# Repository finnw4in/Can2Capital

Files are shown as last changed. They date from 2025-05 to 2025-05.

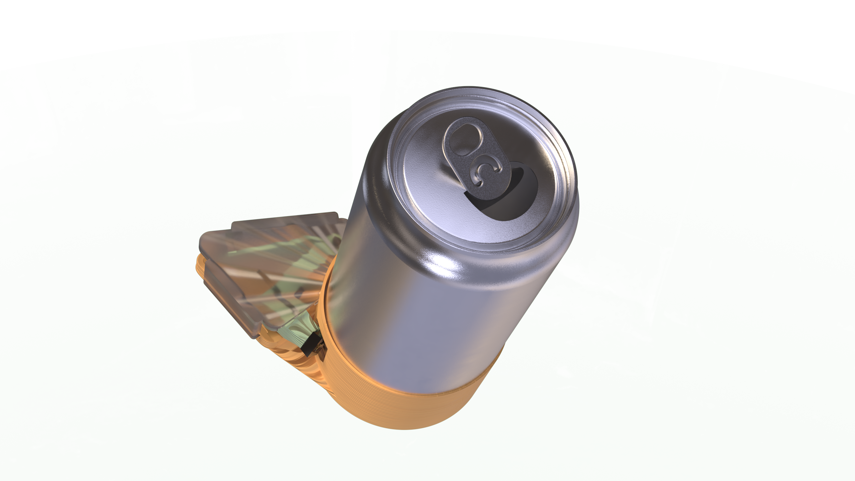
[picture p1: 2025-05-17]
images/BenchTop RenderV3.68.png

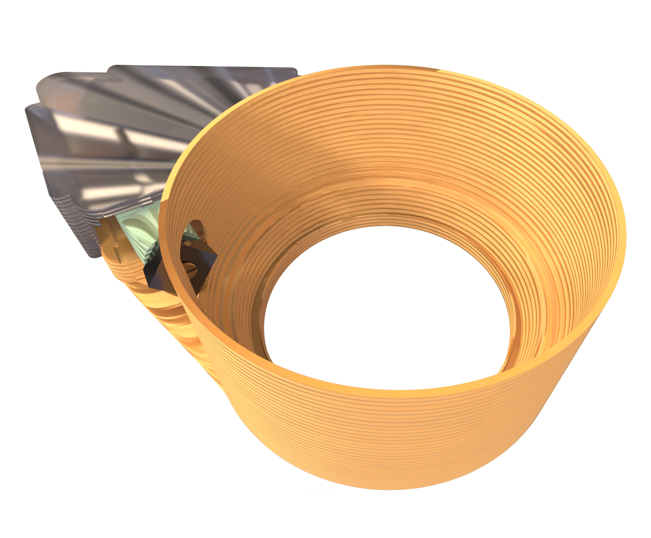
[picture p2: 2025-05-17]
images/BenchTop RenderV3.76.png

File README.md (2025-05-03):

title: Can-2-Capital
Date: 2025-05-03

# Can 2 Capital: A Decentralised Digital Kit

**Can 2 Capital** is a decentralised digital kit that enables anyone and everyone to turn waste aluminium cans into something valuable that can be sold, traded, or kept.

### How Does It Differ?
Can 2 Capital differs from traditional industrial aluminium recycling as it seeks to return **profit to the user**, not the producer.

---

### Powered by YOU:
- **100 Joules of Human Effort**
- **50g of PETG & Carbide Insert**

---

### Key Benefits:
- **28x Increase in Recycling Collection Efficiency**
- **Recycle with 99.8% Less Energy** than industrial recycling

---

Join the movement and make a difference with **Can 2 Capital** today!

## Phase One Download Files

- [Download 3DM Files](https://github.com/finnw4in/Can2Capital/tree/main/3dm-files)

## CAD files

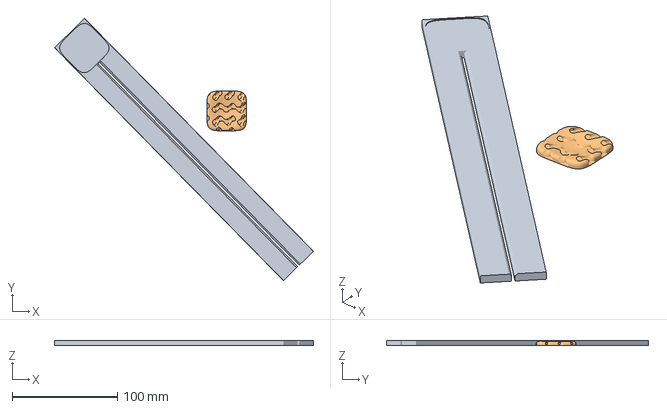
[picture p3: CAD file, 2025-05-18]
3dm-files/Can Finger Model.3mf
245.8 x 249.1 x 5.00 mm
Wain, F, Phase 1, Can-2-Capital-Stripper Can Finger.stl_10
Wain, F, Phase 1, Can-2-Capital-Stripper Can Finger.stl_11

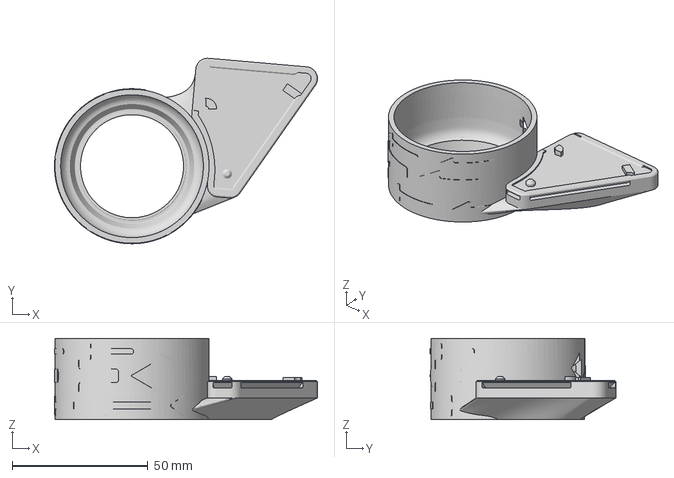
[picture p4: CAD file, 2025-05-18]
3dm-files/53mm Slim.3mf
97.0 x 68.5 x 30.0 mm

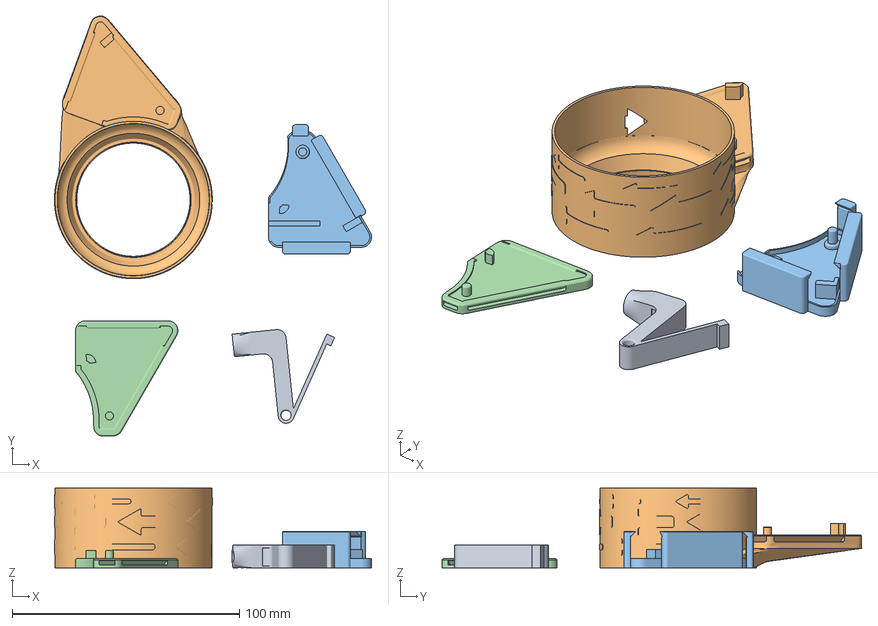
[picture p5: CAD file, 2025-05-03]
3dm-files/Can-2-Capital-Stripper Tool-V11.3mf
139.6 x 184.9 x 35.0 mm
V10.5 Spring Mech v1 v2
V11.5 Lower .step
v11 plate v1.step

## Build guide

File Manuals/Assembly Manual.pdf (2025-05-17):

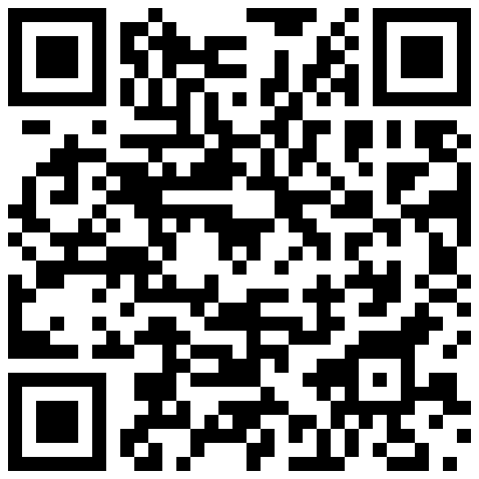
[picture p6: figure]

# Can 2 Capital Can Stripper Assembly Guide ENGLISH

3

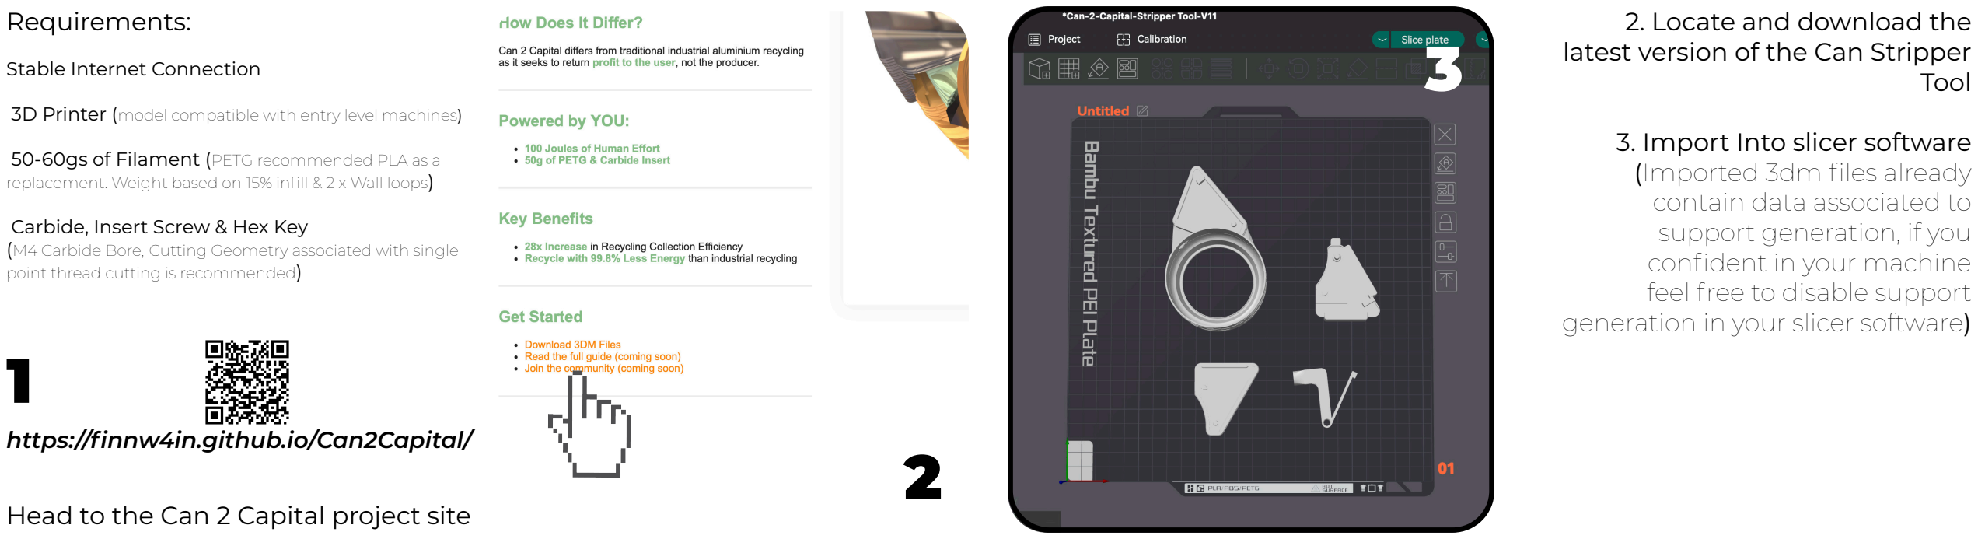
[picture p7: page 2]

2. Locate and download the latest version of the Can Stripper Tool
3. Import Into slicer software (Imported 3dm files already

contain data associated to support generation, if you confident in your machine
feel free to disable support generation in your slicer software

)
2

https://finnw4in.github.io/Can2Capital/ 1

Head to the Can 2 Capital project site

Requirements:

Stable Internet Connection

3D Printer (model compatible with entry level machines )

50-60gs of Filament (PETG recommended PLA as a replacement. Weight based on 15% infill & 2 x Wall loops

)

Carbide, Insert Screw & Hex Key (M4 Carbide Bore, Cutting Geometry associated with single

point thread cutting is recommended

)

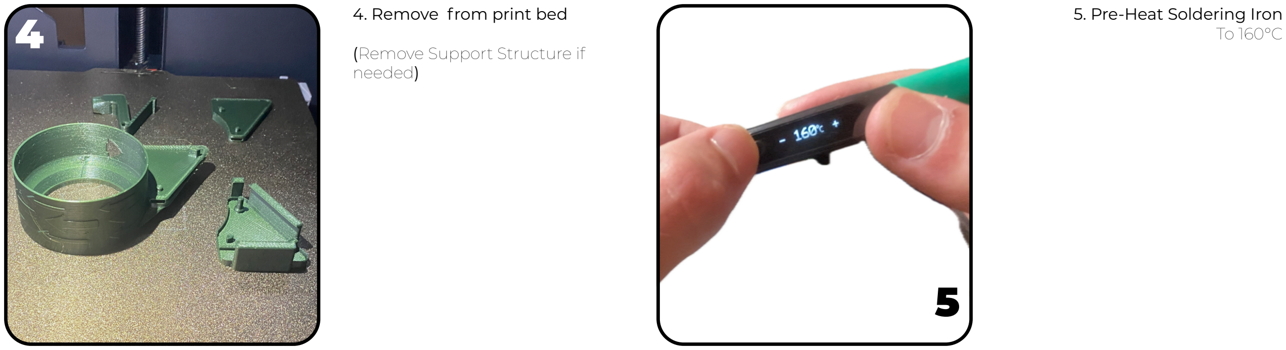
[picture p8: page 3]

4. Remove from print bed

(Remove Support Structure if needed)

5. Pre-Heat Soldering Iron

### 4 To 160°C

5

6

7

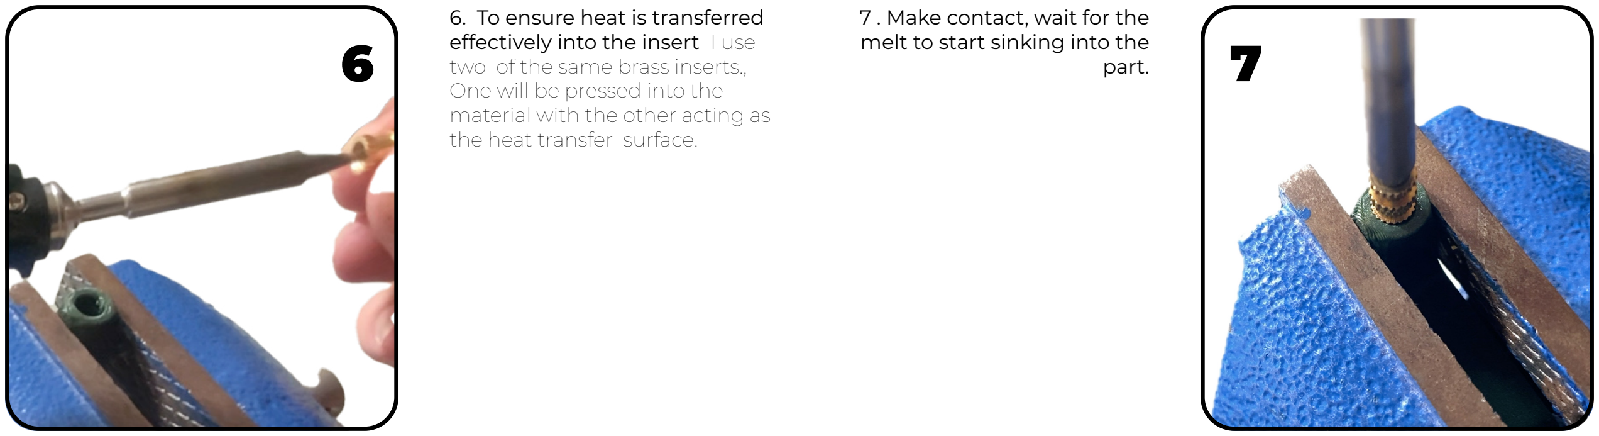
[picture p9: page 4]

6. To ensure heat is transferred effectively into the insert I use two of the same brass inserts., One will be pressed into the material with the other acting as the heat transfer surface.

7 . Make contact, wait for the melt to start sinking into the part.

9

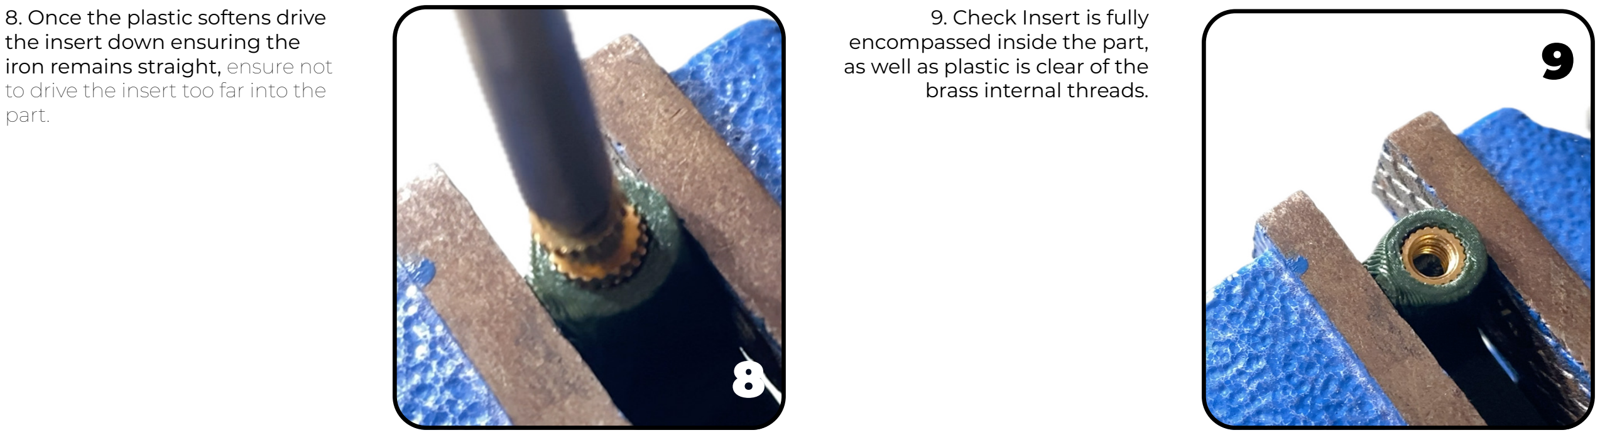
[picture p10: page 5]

8

8. Once the plastic softens drive the insert down ensuring the iron remains straight, ensure not to drive the insert too far into the part.
9. Check Insert is fully
encompassed inside the part, as well as plastic is clear of the brass internal threads.

10 11

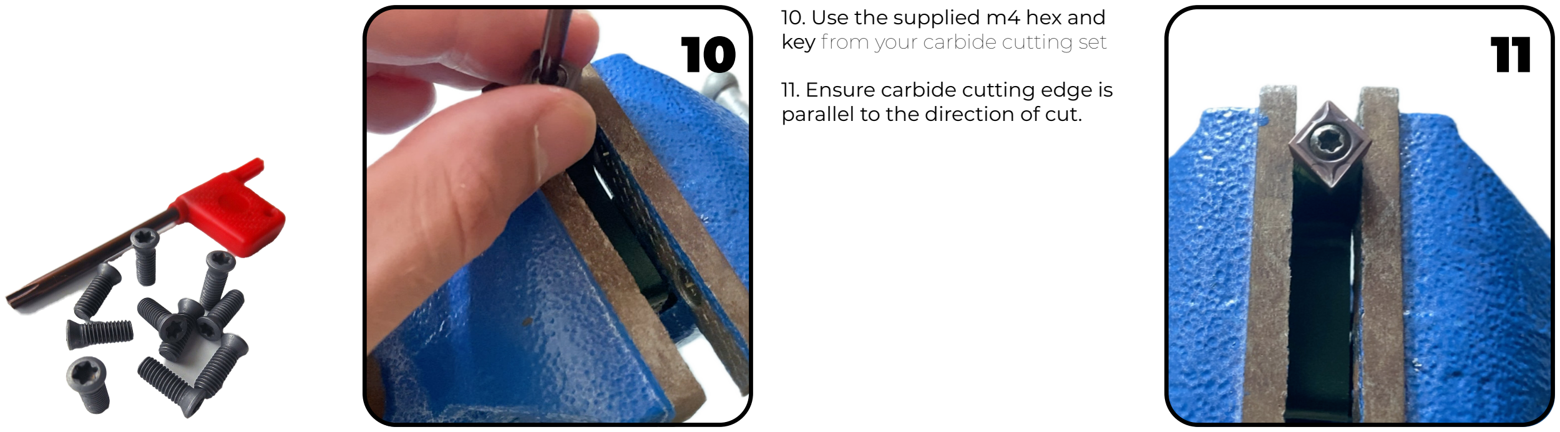
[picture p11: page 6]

10. Use the supplied m4 hex and key from your carbide cutting set
11. Ensure carbide cutting edge is parallel to the direction of cut.

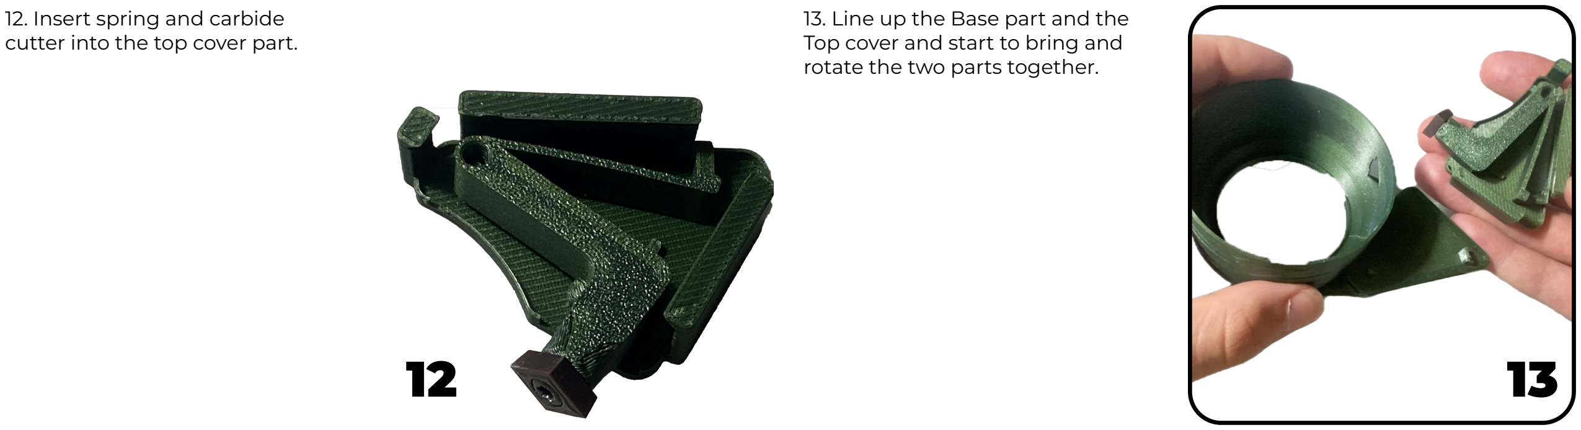
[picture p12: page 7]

12 13

12. Insert spring and carbide cutter into the top cover part.
13. Line up the Base part and the Top cover and start to bring and rotate the two parts together.

14 15

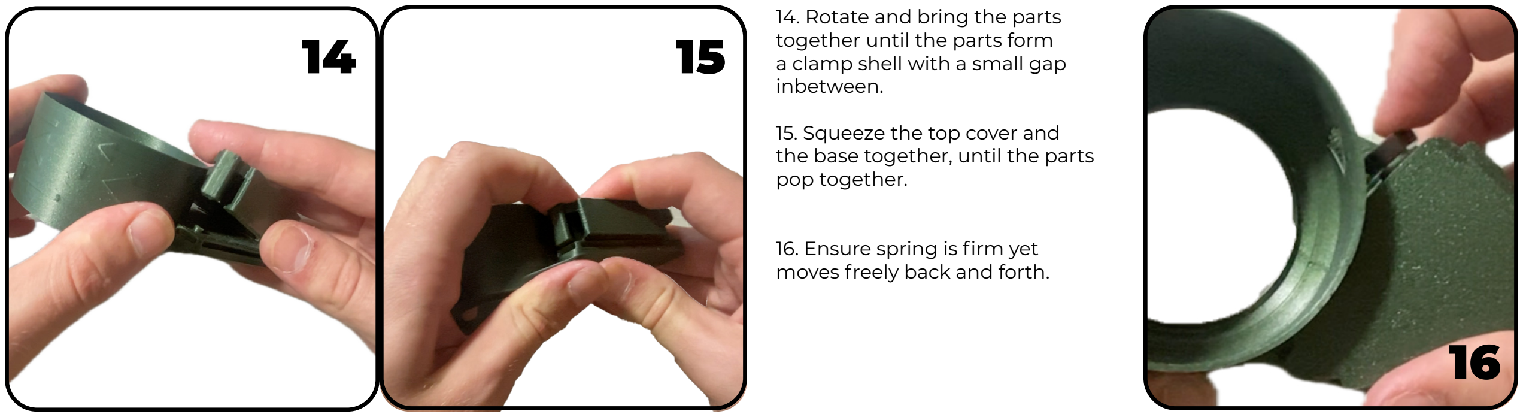
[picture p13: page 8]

16

14. Rotate and bring the parts together until the parts form a clamp shell with a small gap inbetween.
15. Squeeze the top cover and the base together, until the parts pop together.
16. Ensure spring is firm yet moves freely back and forth.

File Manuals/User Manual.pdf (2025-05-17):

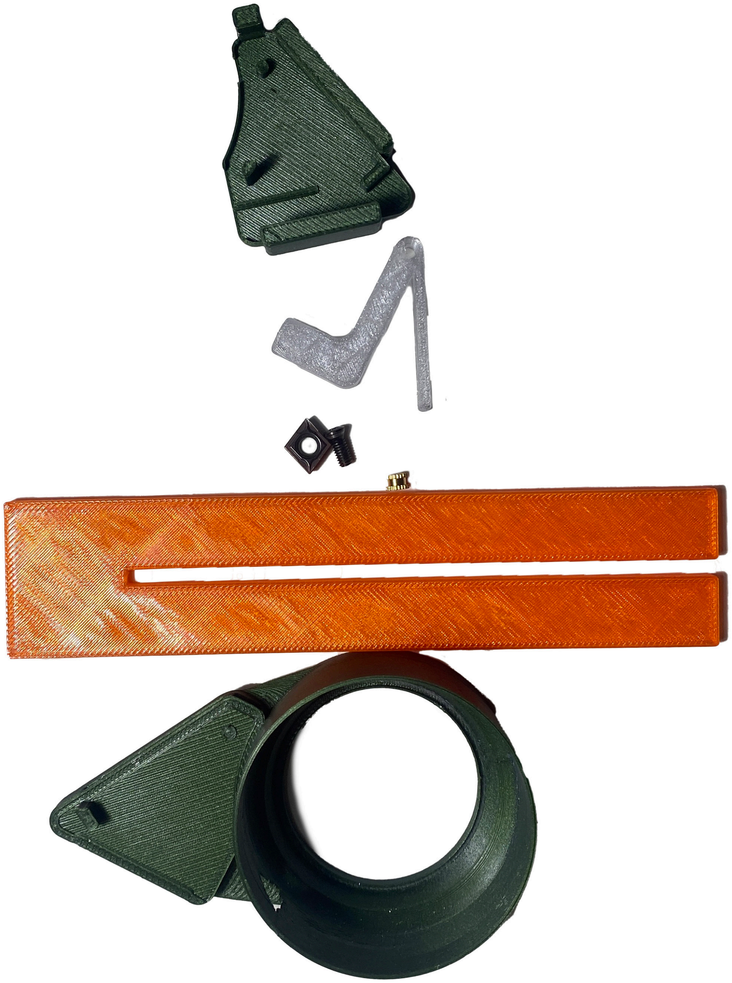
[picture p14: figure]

Top Cover

Compliant Spring Arm

Carbide Insert &
Hex Screw

m4 Threaded Insert

Can Finger

Can Curve Base

## Can 2 Sheet User instruction manual English

1
3

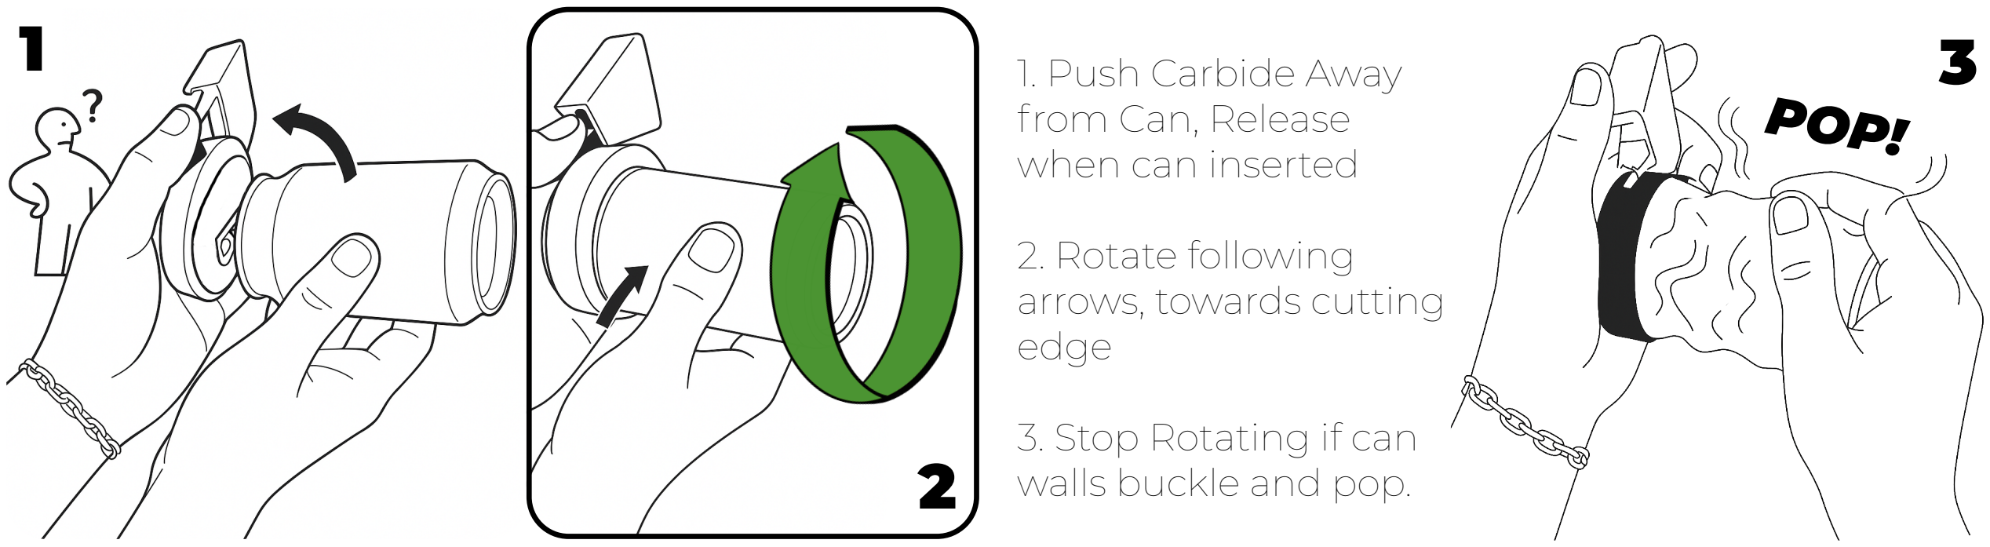
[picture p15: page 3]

2

## POP!

1. Push Carbide Away
from Can, Release
when can inserted
2. Rotate following
arrows, towards cutting
edge
3. Stop Rotating if can
walls buckle and pop.

4
6

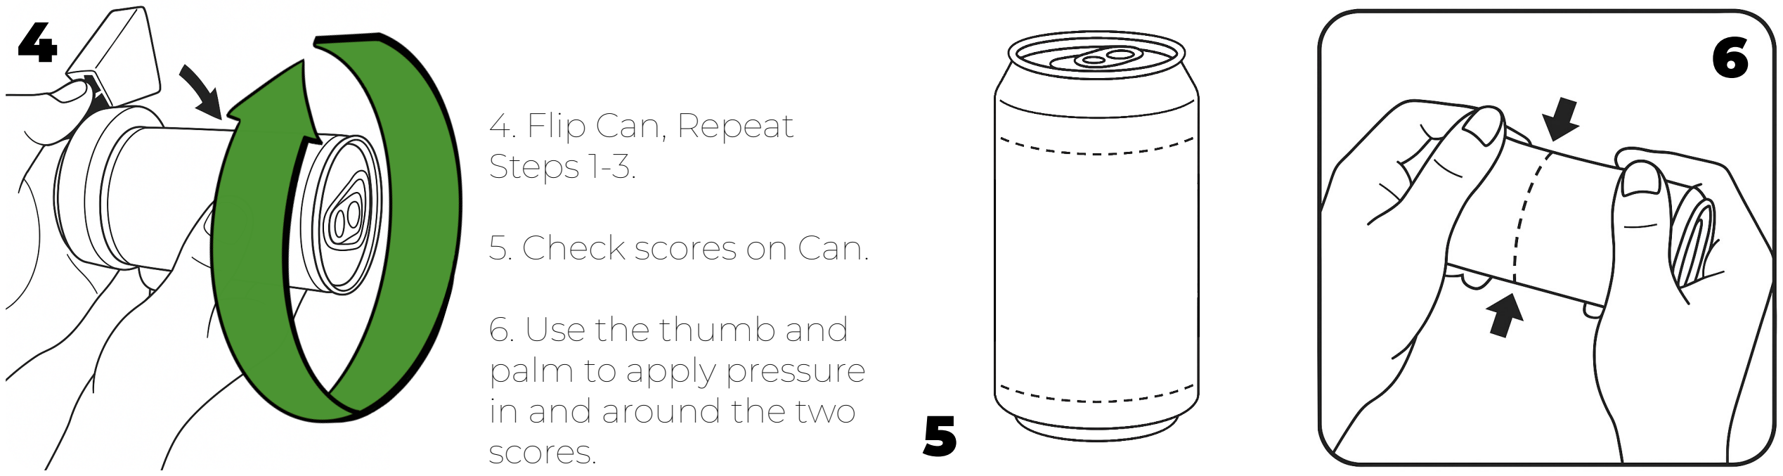
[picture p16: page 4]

4. Flip Can, Repeat
Steps 1-3.
5. Check scores on Can.
6. Use the thumb and
palm to apply pressure
in and around the two
scores.

5

8

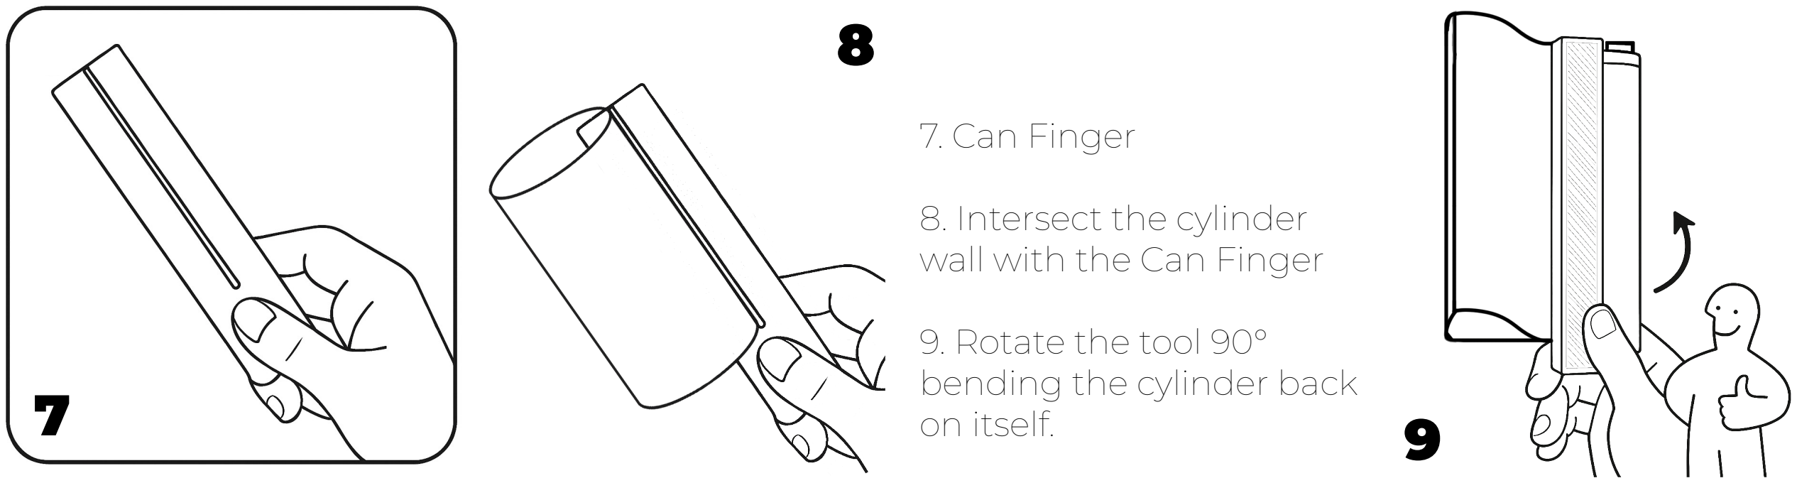
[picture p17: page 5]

7
9
7. Can Finger
8. Intersect the cylinder
wall with the Can Finger
9. Rotate the tool 90°
bending the cylinder back
on itself.

12

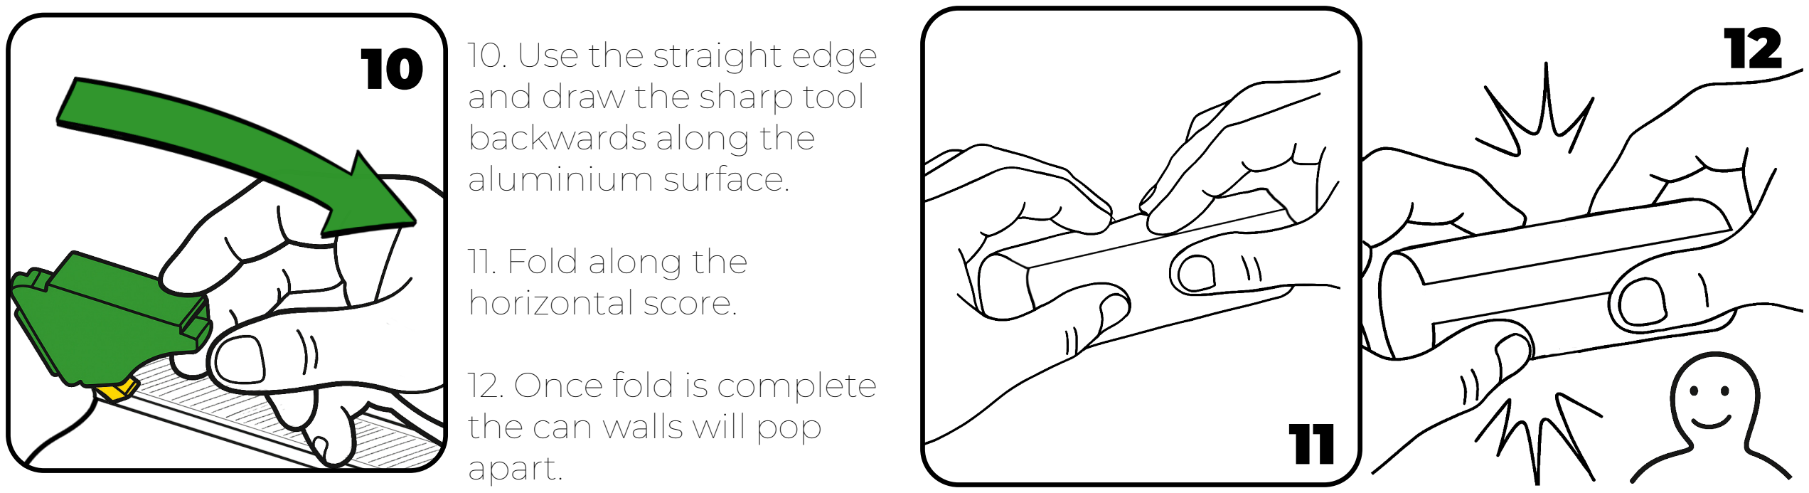
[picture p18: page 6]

10 10. Use the straight edge and draw the sharp tool
backwards along the
aluminium surface.
11. Fold along the
horizontal score.
12. Once fold is complete
the can walls will pop
apart. | 11

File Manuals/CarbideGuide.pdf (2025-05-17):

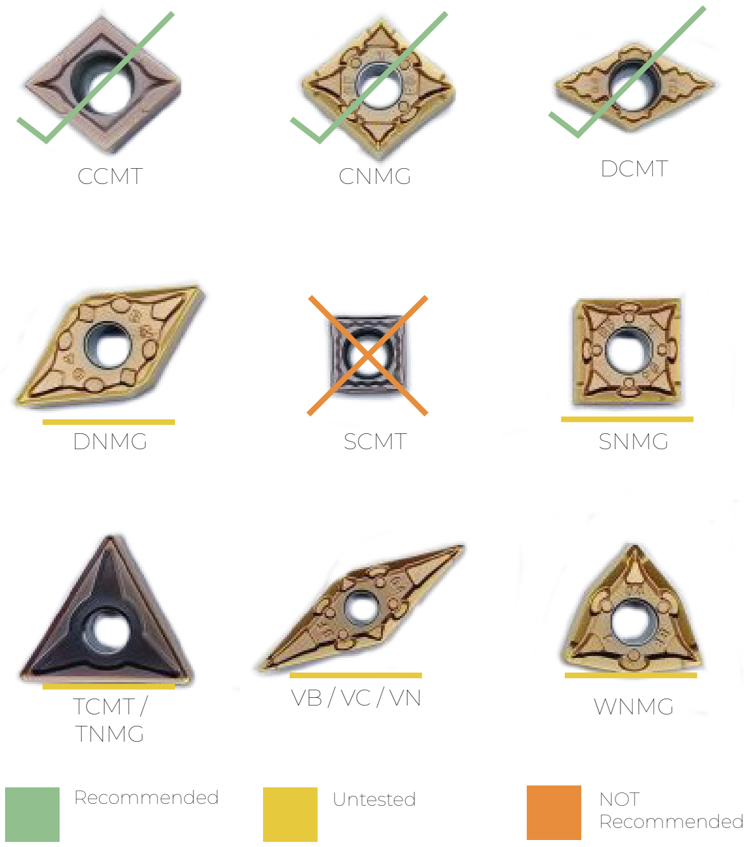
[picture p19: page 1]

CCMT | CNMG | DCMT
DNMG | SCMT | SNMG
TCMT / | VB / VC / VN | WNMG
TNMG
Recommended | Untested | NOT Recommended
